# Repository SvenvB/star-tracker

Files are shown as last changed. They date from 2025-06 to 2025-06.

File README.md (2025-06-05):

# DIY Sidereal Star Tracker for the EQ-13 mount (Orion SpaceProbe 130ST telescope)

I'm using the [Orion SpaceProbe 130ST telescope](https://www.highpointscientific.com/orion-spaceprobe-130st-short-tube-eq-reflector-telescope) with a [ZWO ASI224MC](https://www.zwoastro.com/product/zwo-asi224mc/) CMOS imaging camera and enjoy deep-sky imaging without breaking the bank. I got the telescope right before Orion ceased to exist and was therefore unable to purchase their [electronic tracking drive](https://www.amazon.com/Orion-Electronic-Tracking-Drive-Mount/dp/B0B9GHRXKY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) for the [EQ-13 mount](https://optcorp.com/products/orion-eq-13-equatorial-telescope-mount-and-tripod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) that came with the telescope. As a result, I decided to make a simple driver myself. The total price was around $50 (I am not fully sure since I had various components already in house), with the cost dominated by the stepper motor (~$30).

The star tracker is powered by a 12 V source using 8× 1.5 V AA batteries. This power source is also used for my [Flat Frame Light Diffuser](https://github.com/SvenvB/Flat-frame-light-diffuser). The battery pack lasts at least one or two full nights imaging.

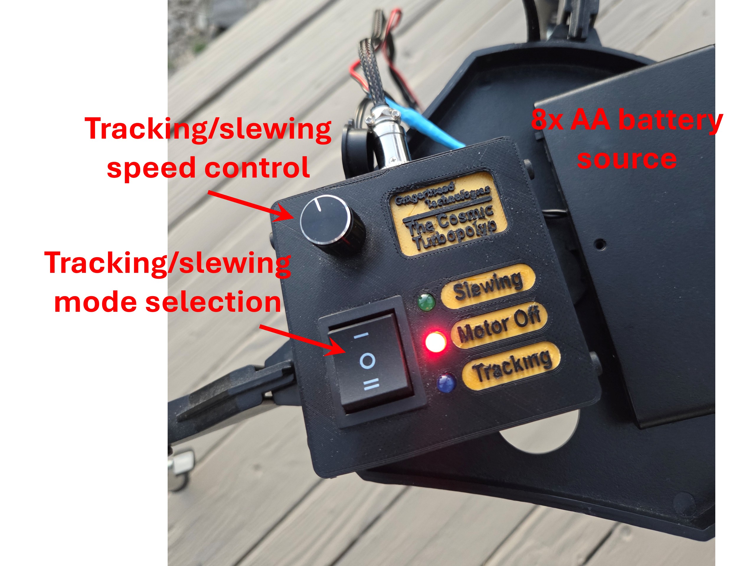
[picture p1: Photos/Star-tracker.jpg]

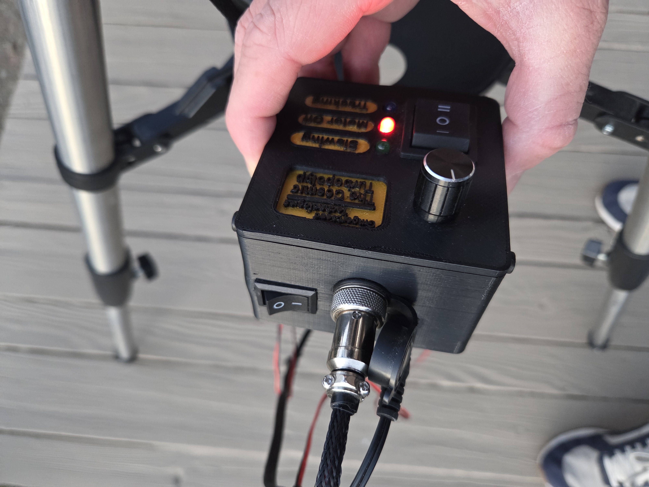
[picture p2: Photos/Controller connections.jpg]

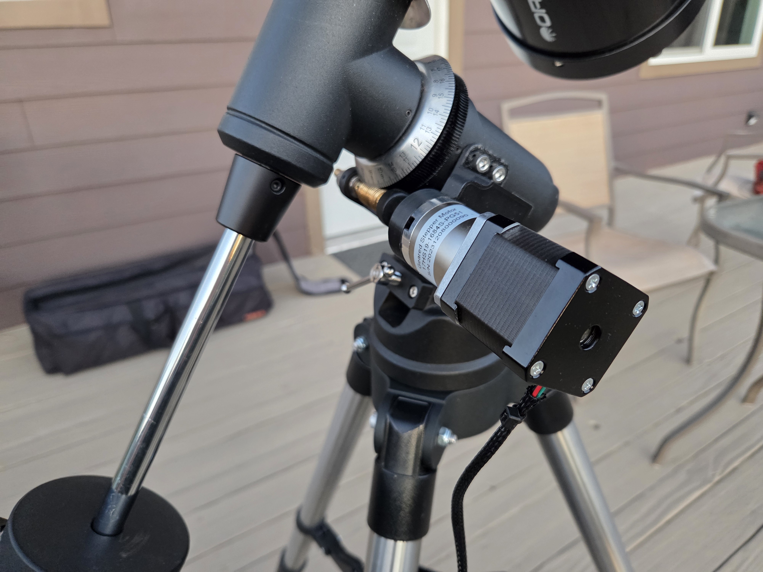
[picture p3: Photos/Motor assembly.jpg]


With this motor, I’ve been able to consistently achieve good tracking for exposure times of up to 5 seconds without noticeable star trailing. For example, see the stacked result of a 140-frame, 5-second exposure of the M27 Dumbbell Nebula:

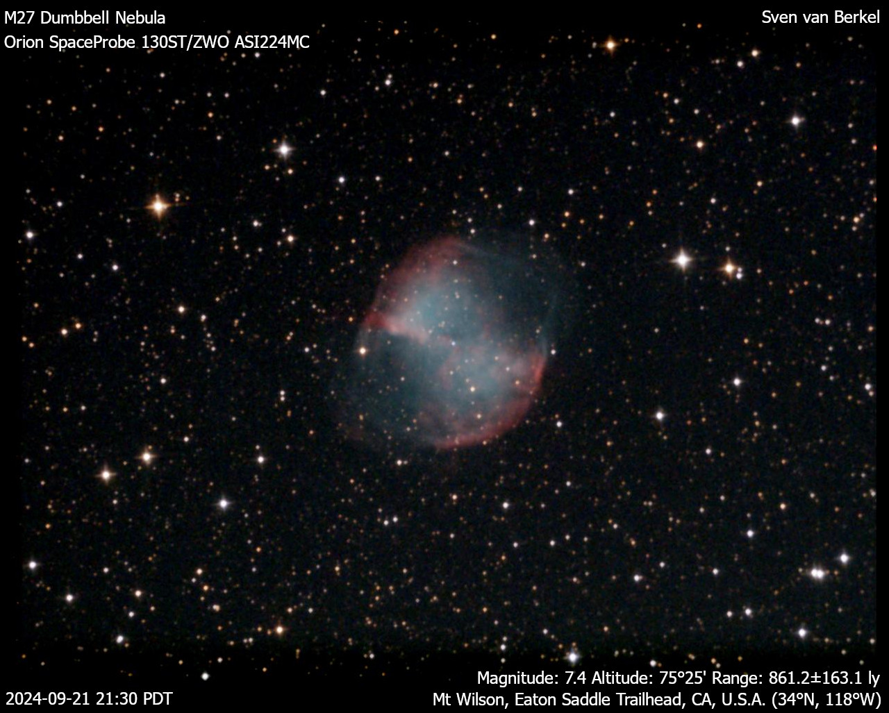
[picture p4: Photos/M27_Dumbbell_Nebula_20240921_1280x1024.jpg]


The exposure time can be pushed up to 20 seconds, as I tried recently when imaging the M51 Whirlpool Galaxy and M104 Sombrero Galaxy. At this exposure time, I had to discard about 50% of the frames due to noticeable star trailing, but the results were still quite nice:

**M51 Whirlpool Galaxy using 49 frames at 20-second exposure:**

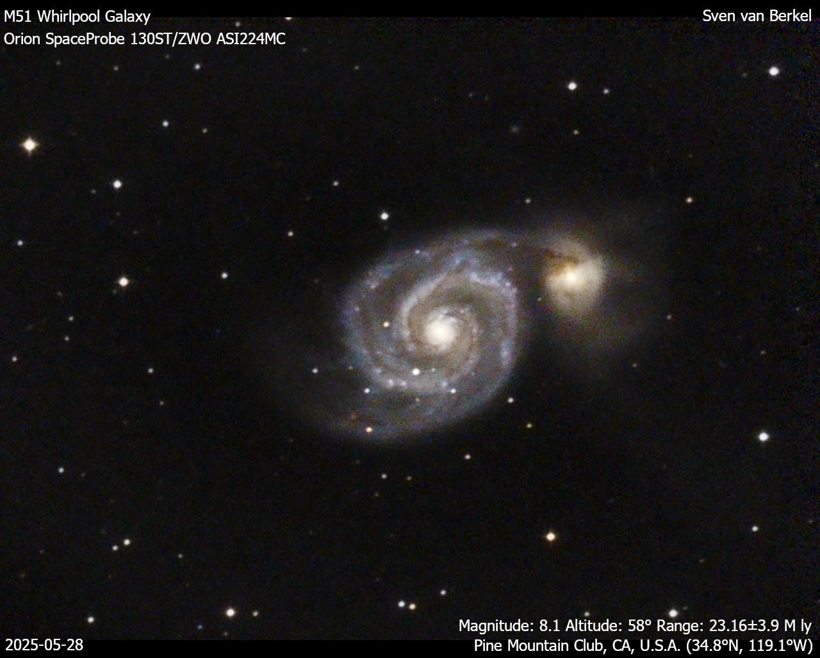
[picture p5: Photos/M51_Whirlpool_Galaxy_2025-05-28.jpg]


**M104 Sombrero Galaxy using 162 frames at 20-second exposure:**

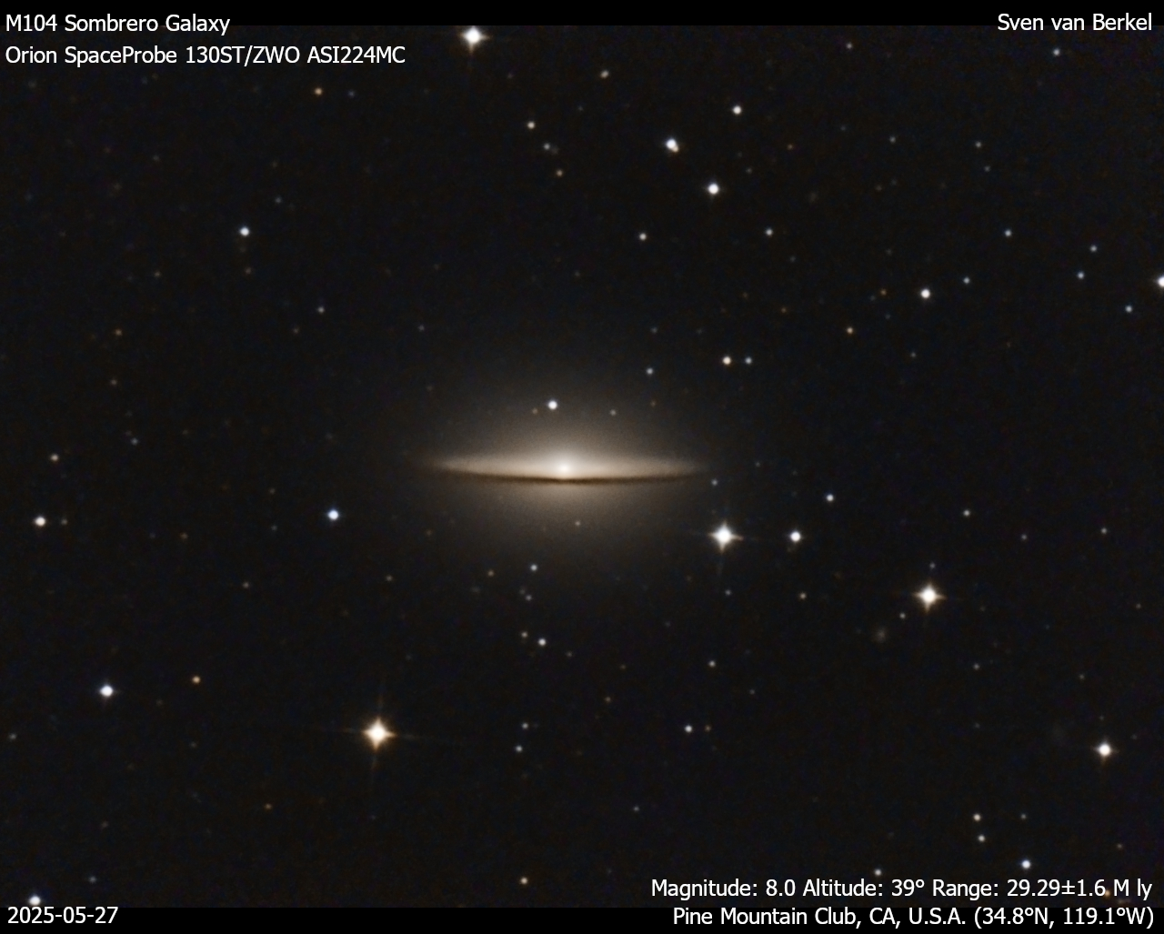
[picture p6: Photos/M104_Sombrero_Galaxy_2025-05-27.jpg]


Keep in mind that the EQ-13 mount is very flimsy, so the effective tracking speed can be inconsistent and occasionally needs to be fine-tuned with the rotary encoder. Properly balancing the telescope with the counterweight is also important.

The star tracker has two modes: **Tracking** (sidereal speed) and **Slewing** (for quick repointing). Both speeds can be fine-tuned with the rotary encoder. Clicking the encoder resets the speed to its default value.

---

## Materials

* **Stepper motor** – The [17HS19-1684S-PG51](https://www.omc-stepperonline.com/nema-17-stepper-motor-bipolar-l-48mm-w-gear-ratio-51-1-planetary-gearbox-17hs19-1684s-pg51) has an 51:1 gear ratio Planetary Gearbox and 0.035 deg / step. 
* **[A4988 stepper motor driver](https://www.aliexpress.us/item/3256805793855652.html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)** - with heatsink  
* **[Arduino Nano](https://www.aliexpress.us/item/3256805941736729.html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)**  
* **KY-040 Rotary Encoder** - with clickable switch
* **[AMS1117-5.0V voltage regulator](https://www.aliexpress.us/item/3256803404676437.html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)**
* **100 uF radial electrolytic capacitor** - for A4988 protection
* **4x through hole 5mm LEDs** - Three to indicate the motor mode and one to indicate that the controller is powered.
* **6x SMD 0805 resistors** - 4x for LED loading (~1 kOhm) and 2x pull-up resistors for the switch (>5 kOhm).
* **2A glass tube fuse and [fuse holder](https://www.amazon.com/dp/B074N1NMMX?ref_=ppx_hzsearch_conn_dt_b_fed_asin_title_1)** - for A4988 protection. The holder has 15mm pin spacing and can hold a 5x20mm fuse.
* **[5.5x2.1mm DC barrel jack](https://www.amazon.com/dp/B081DYQSC9/ref=pe_386300_440135490_TE_simp_item_image?th=1)** - for controller power supply
* **[4 pin aviation plug](https://www.amazon.com/dp/B07ZP725YD/ref=pe_386300_440135490_TE_simp_item_image)** - for connecting the stepper motor
* **[3 position rocker switch](https://www.aliexpress.us/item/2251832521009333.html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)** - for motor mode selection
* **2 position rocker switch** - for controller power ON/OFF
* **2x 5-pin JST connectors** - male and female for connecting the rotary encoder and Switch-and-LED board
* **2x 2-pin JST connectors** - male and female for connecting the power rocker switch and power to the Switch-and-LED board.
* **4-pin JST connector**  - male and female for connecting the aviation plug.
* **[8x AA battery holder](https://www.amazon.com/dp/B09LTSNJTW/ref=pe_386300_440135490_TE_simp_item_image)** - with 5.5x2.1mm Male Jack Connector
* **various screws** - to mount the PCBs to the casing and top-plate, to mount the top-plate to the casing, to connect the stepper motor to the 3D-printed mount, to prevent the 3D-printed coupling piece from slipping on the worm gear shaft, to connect the 3D-printed mount to the EQ-13 body.
* **3D printer and filament** - for the motor mount and controller box.

**Optional**
* **Capacitors** - at the output of the voltage regulator to reduce power supply noise. I used a 10 uF radial and 100 nF + 10 nF ceramic disc capacitors in parallel. 
* **Cable sleeve** - to organize the stepper motor wires.
* **3-pin screw terminal** - mounted on the switch-and-LED board, to easily connect and disconnect the 3-position rocker switch.

---

## Instructions

### 1. Calculate Stepper Motor Requirements

- Stepper motors are highly accurate and provide high torque, making them ideal for this application. A typical stepper motor has 200 steps per revolution (1.8°/step).
- I tested that the Right Ascension (RA) knob on the EQ-13 mount must be rotated about 5.5 times to move 1 hour in RA. This corresponds to roughly 132 revolutions over 24 h in RA, i.e., a worm gear ratio of 132:1.
- One sidereal day is 23h 56m 4s, or 86,164 seconds. Therefore, the worm gear should rotate at ~0.55°/s. Since a typical stepper motor would move only once every 3+ seconds at this rate, a gearbox is needed.
- Choosing a low gear ratio results in jerky tracking, while too high a gear ratio limits slewing speed.
- I chose the [17HS19-1684S-PG51](https://www.omc-stepperonline.com/nema-17-stepper-motor-bipolar-l-48mm-w-gear-ratio-51-1-planetary-gearbox-17hs19-1684s-pg51) stepper motor with a 51:1 gearbox. This gives a tracking speed of ~15.6 steps per second, which I would not recommend going below.

**RA worm gear visible in the picture below:**

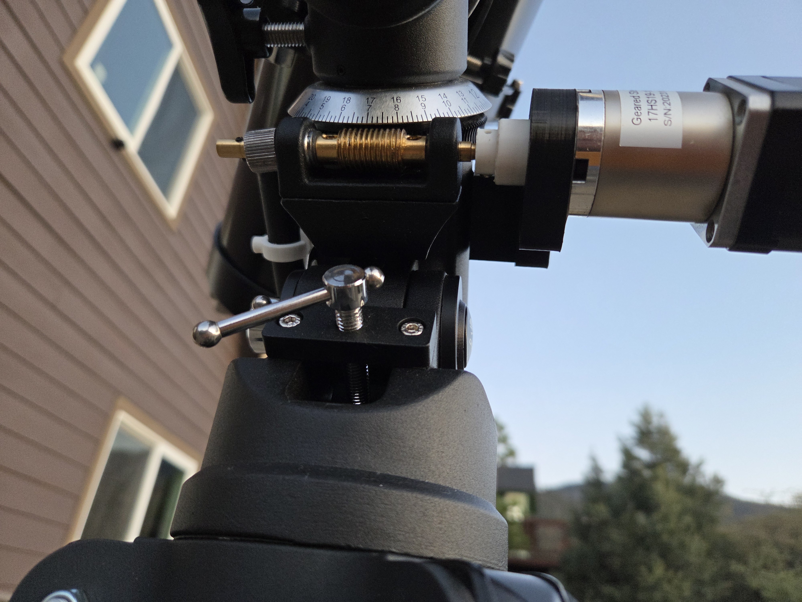
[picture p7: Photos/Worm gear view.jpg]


---

### 2. Electrical Design

The controller uses two PCBs:

1. **Switch-and-LED board** – Mounted to the front plate. This board connects to the 3-position rocker switch, integrates pull-up resistors, and drives LEDs indicating the motor mode. It is reused from another project that daisy-chains the power pins two multiple boards.
2. **Controller board** – Mounted to the bottom of the casing. This board contains the Arduino, stepper motor driver, and supporting components.

Boards were designed in KiCAD. Gerber files are attached, and PCBs were ordered via JLCPCB.

#### Switch-and-LED Board
* The pin-headers shown below are not needed. You can directly solder the cables to the PCB, as is shown in the *Assembled Control Box* photograph in Section 4 below. 
* The schematic indicates LED resistors of 470 Ohm. However, I have found that the LEDs are too bright with those values. I recommend increasing them. 

*KiCAD Schematic:*
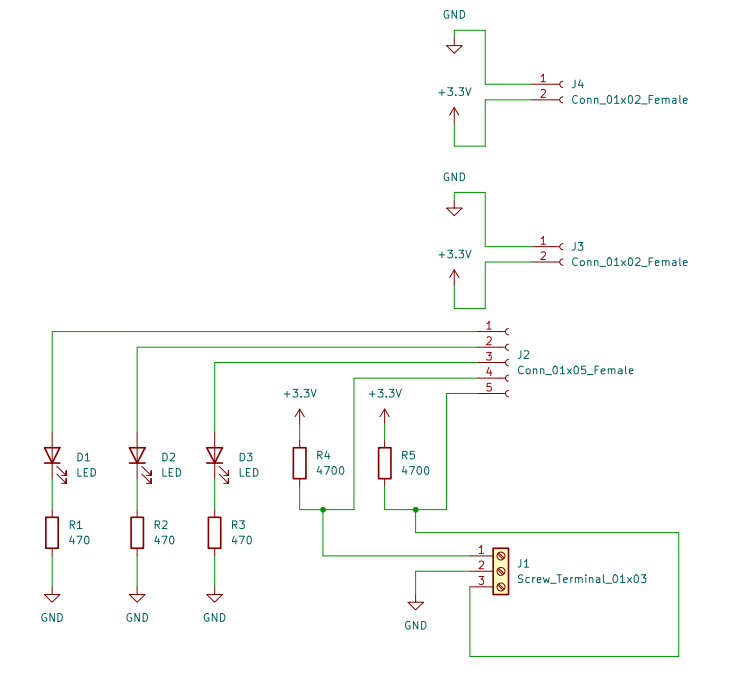
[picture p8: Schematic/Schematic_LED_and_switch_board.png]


*KiCAD 3D View:*
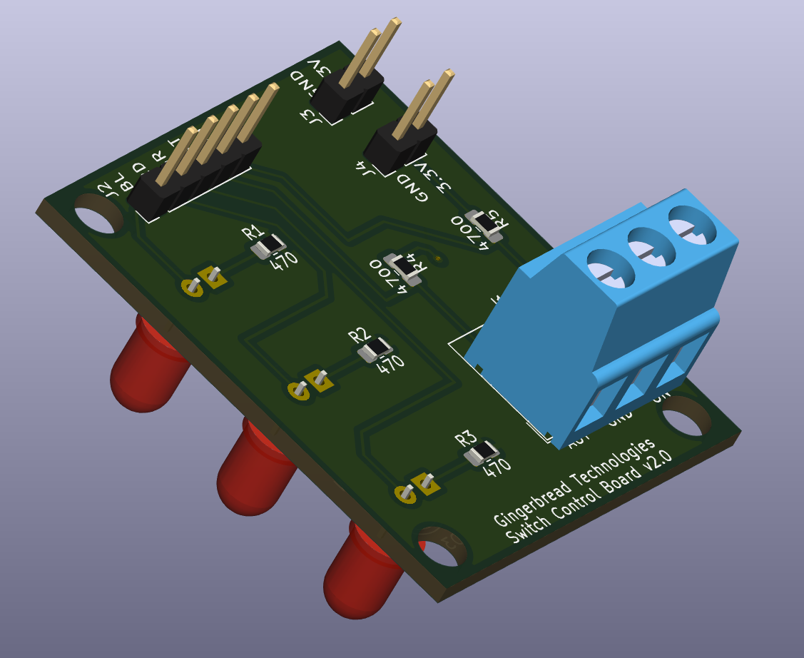
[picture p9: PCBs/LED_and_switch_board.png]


#### Controller Board

- Be sure to include the 100 µF capacitor. The A4988 can produce voltage spikes due to back-EMF from the stepper motor’s inductance. This capacitor helps absorb those spikes, protecting the driver. Place the capacitor as close to the driver as is possible.
- The capacitors at the AMS1117 output are optional.
- Use the method described [here](https://www.pololu.com/product/1182) to limit the A4988 current to your motor’s rated current (1.68 A/phase for mine).
- I have not employed microstepping to increase the number of steps per second. The motor might operate more smoothly if we half the step. However, it will mean tighter timing and more processing overhead for the Arduino, and a reduced torque per microstep. If the mount is imbalanced the torque might not be adequate. Something to be tested.

*KiCAD Schematic:*
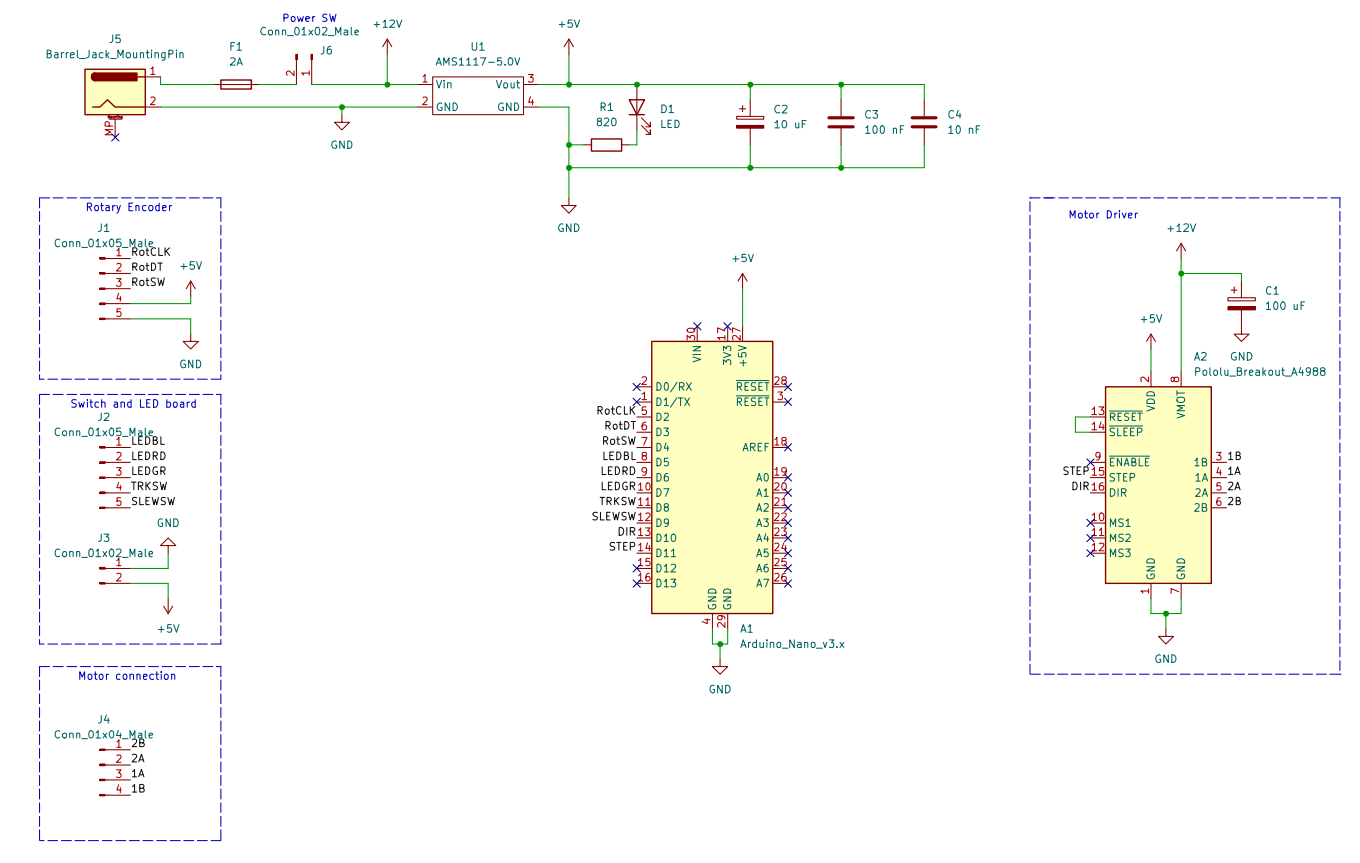
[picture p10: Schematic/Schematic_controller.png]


*KiCAD 3D View:*
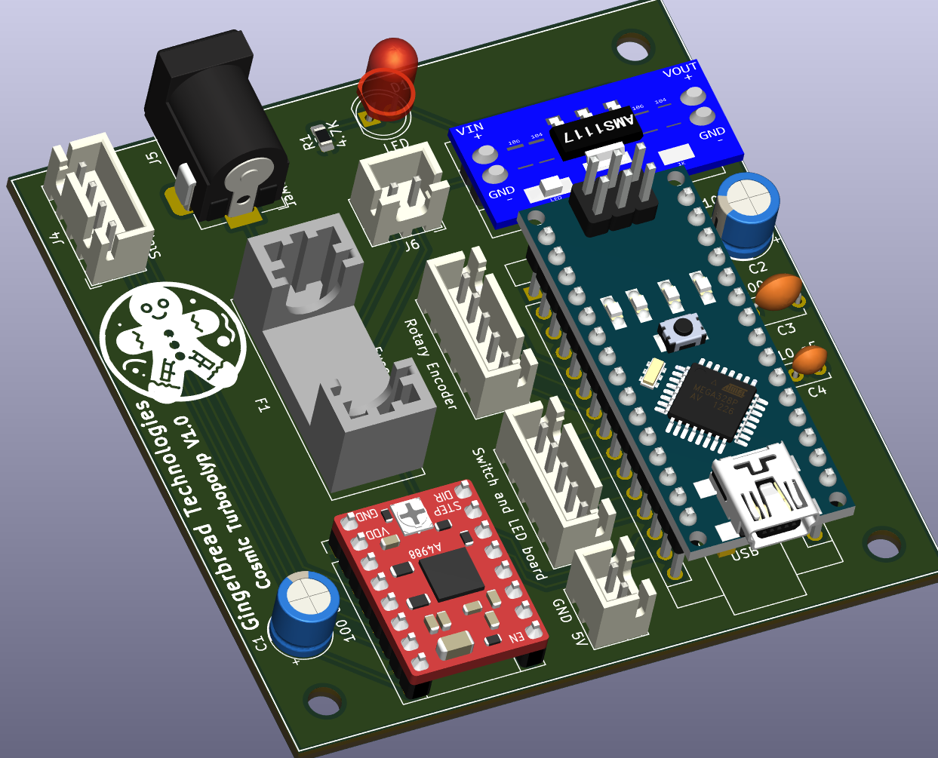
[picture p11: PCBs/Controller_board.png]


*Assembled Controller Photo:*
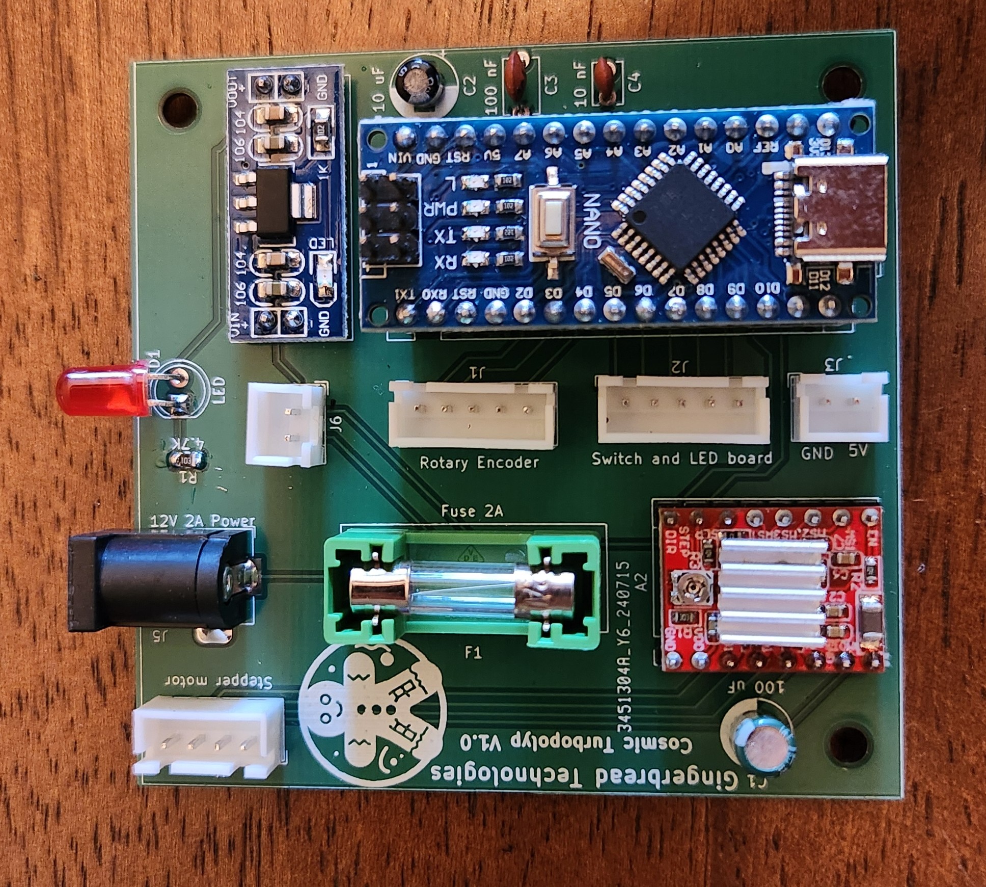
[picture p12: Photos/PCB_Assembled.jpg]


---

### 3. CAD Design

- The control box and motor mount were designed in FreeCAD. Design files and .STLs are attached.
- The coupling piece between the stepper motor and worm gear shaft (green part in the image) must fit very tightly to avoid backlash.
- You will need a screw to mate the coupling piece to the worm gear shaft. 

*FreeCAD View – Control Box (Closed):*
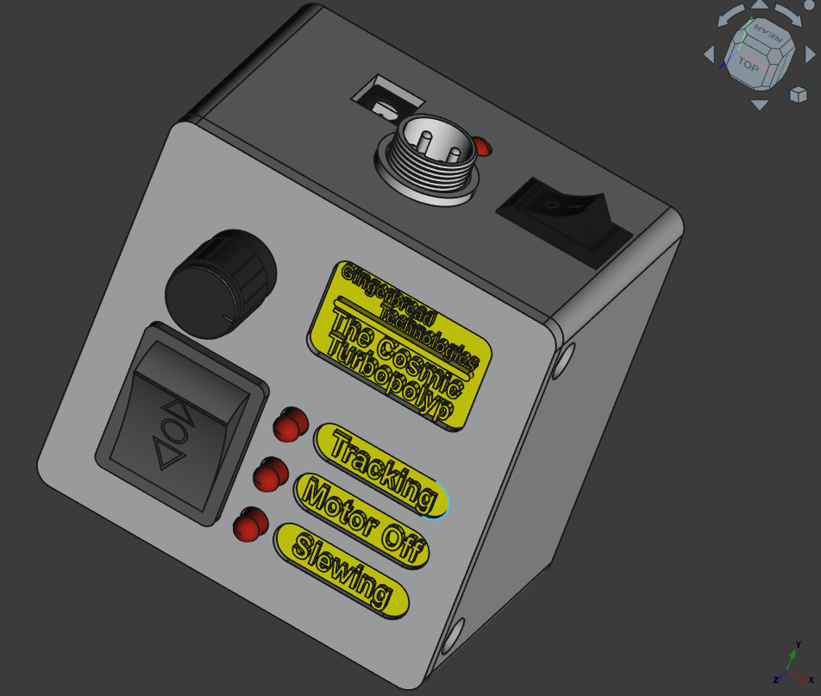
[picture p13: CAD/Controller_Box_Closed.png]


*FreeCAD View – Control Box (Open):*
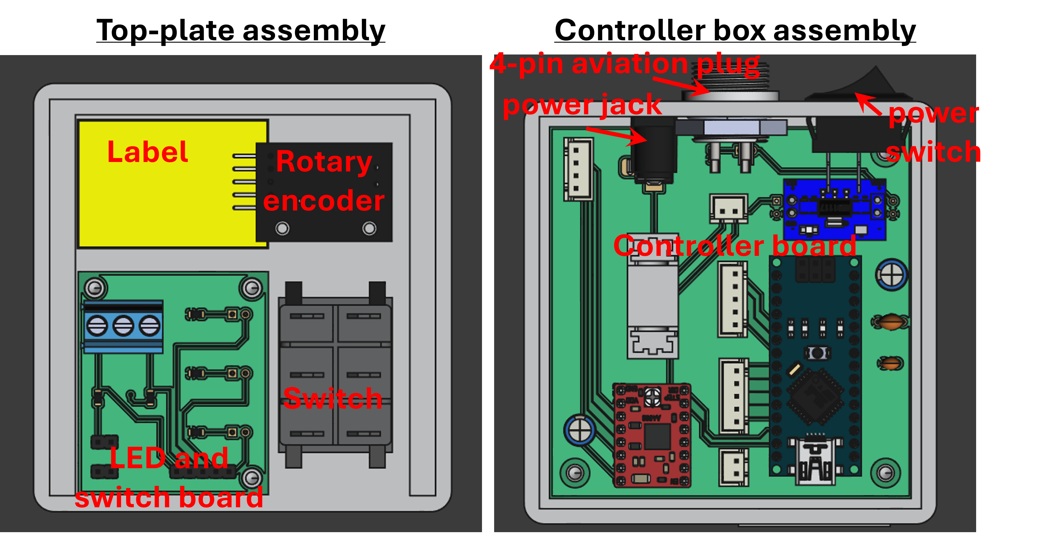
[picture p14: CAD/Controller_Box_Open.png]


*FreeCAD View – Motor Mount:*
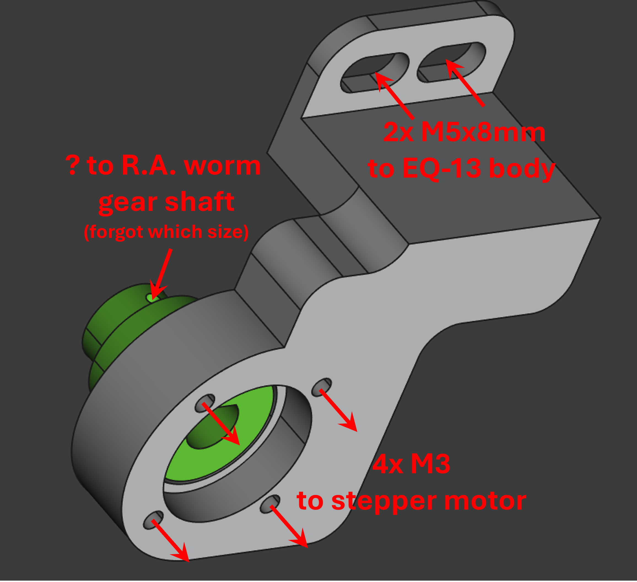
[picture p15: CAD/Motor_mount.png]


---

### 4. Assembly

- Mount the PCBs to the casing and top plate using screws.
- Avoid contact between wires and the heatsink of the stepper motor driver.

*Assembled Control Box:*
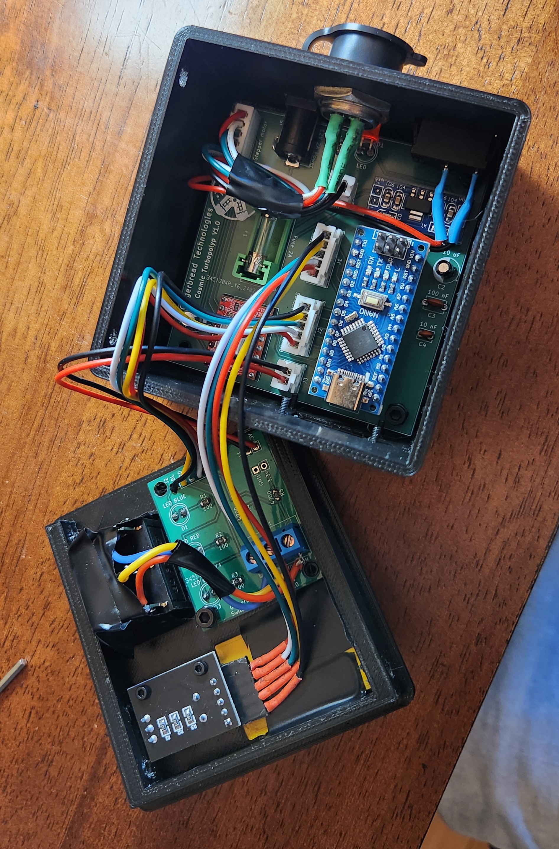
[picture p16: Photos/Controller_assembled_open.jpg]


*Assembled Stepper Motor:*


---

### 5. Arduino Coding and Operation

- The Arduino is programmed using the standard Arduino IDE. Code is available [here](./Arduino/RA_Controller_V3/RA_Controller_V3.ino).
- I found the most stable tracking at 16.3 steps/second, close to the calculated 15.6 steps/sec sidereal speed.
- In **Tracking mode**, each rotary tick changes the speed by ±0.1 steps/sec.
- In **Slewing mode**, each tick changes the speed by ±1× sidereal rate. Slewing is possible in both RA directions.
- Clicking the rotary encoder resets the speed to its default value.

**Clear skies!**

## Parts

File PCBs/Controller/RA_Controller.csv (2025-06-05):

Reference | Value | Datasheet | Footprint | Qty | DNP
A1 | Arduino_Nano_v3.x | http://www.mouser.com/pdfdocs/Gravitech_Arduino_Nano3_0.pdf | Module:Arduino_Nano | 1
A2 | Pololu_Breakout_A4988 | https://www.pololu.com/product/2980/pictures | Module:Pololu_Breakout-16_15.2x20.3mm | 1
C1 | 100 uF | ~ | Capacitor_THT:CP_Radial_D6.3mm_P2.50mm | 1
C2 | 10 uF | ~ | Capacitor_THT:CP_Radial_D6.3mm_P2.50mm | 1
C3 | 100 nF | ~ | Capacitor_THT:C_Disc_D5.1mm_W3.2mm_P5.00mm | 1
C4 | 10 nF | ~ | Capacitor_THT:C_Disc_D3.8mm_W2.6mm_P2.50mm | 1
D1 | LED | ~ | LED_THT:LED_D5.0mm | 1
F1 | 2A | ~ | LED_THT:LED_D5.0mm | 1
J1,J2 | Conn_01x05_Male | ~ | Connector_JST:JST_XH_B5B-XH-A_1x05_P2.50mm_Vertical | 2
J3,J6 | Conn_01x02_Male | ~ | Connector_JST:JST_XH_B2B-XH-A_1x02_P2.50mm_Vertical | 2
J4 | Conn_01x04_Male | ~ | Connector_JST:JST_XH_B4B-XH-A_1x04_P2.50mm_Vertical | 1
J5 | Barrel_Jack_MountingPin | ~ | Connector_BarrelJack:BarrelJack_Horizontal | 1
R1 | 820 | ~ | Resistor_SMD:R_0805_2012Metric_Pad1.20x1.40mm_HandSolder | 1
U1 | AMS1117-5.0V |  | Svens Custom Footprints:AMS1117-5.0V | 1

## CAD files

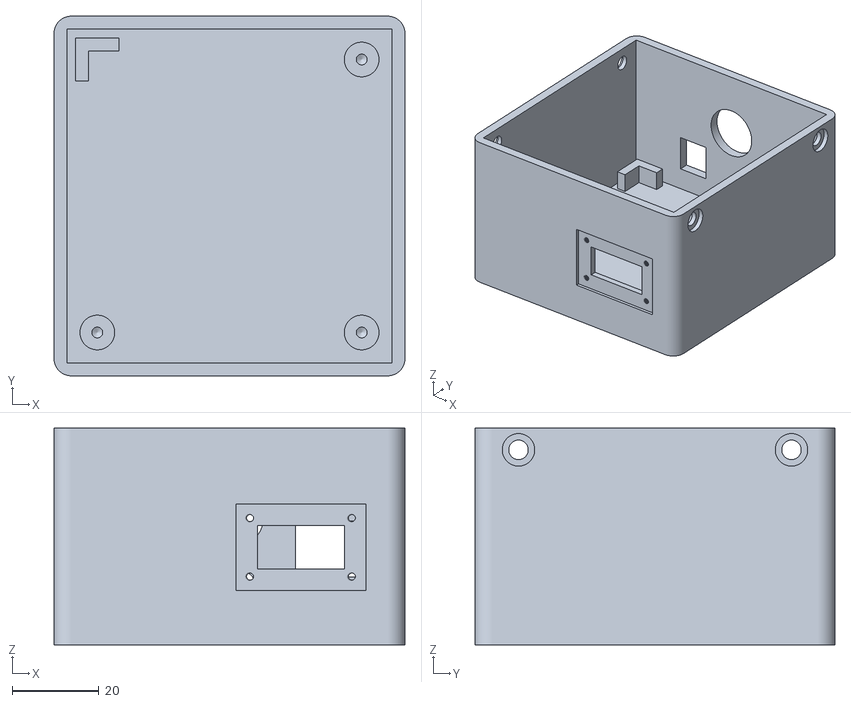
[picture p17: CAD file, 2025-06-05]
CAD/STLs/Main_box.stl
81.0 x 83.0 x 50.0

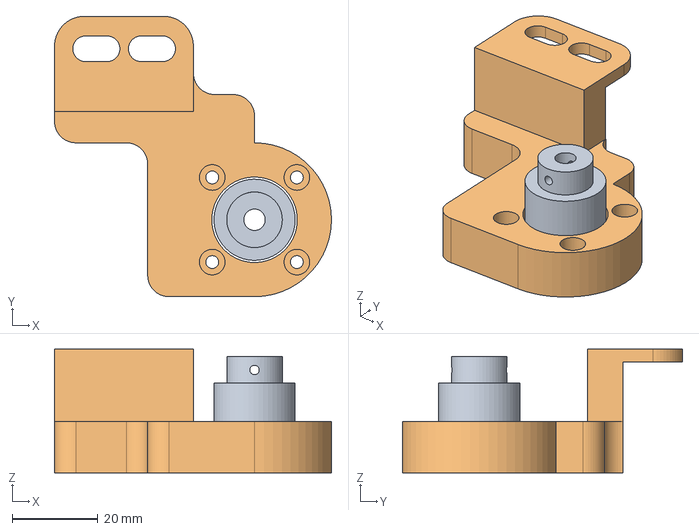
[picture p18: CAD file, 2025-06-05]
CAD/FreeCAD/MotorMount_V2.FCStd
64.8 x 65.6 x 29.0 mm
Stepper_to_RA_knob
Stepper_mount

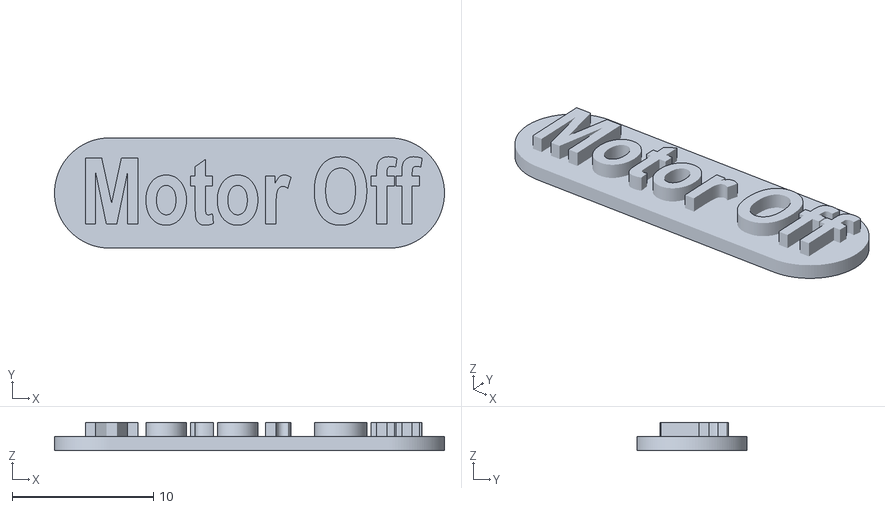
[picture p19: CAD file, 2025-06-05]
CAD/STLs/Motor_off_label.stl
27.6 x 7.80 x 2.00

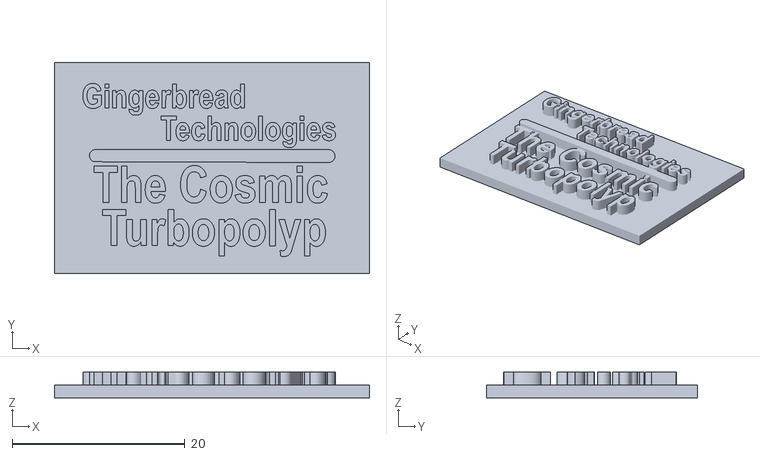
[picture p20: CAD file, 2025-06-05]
CAD/STLs/Gingerbread_label.stl
36.5 x 24.5 x 3.00

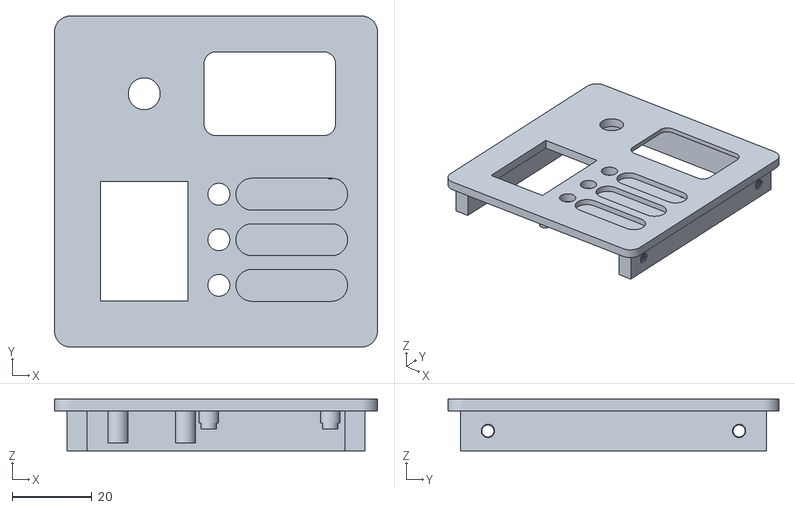
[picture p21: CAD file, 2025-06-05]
CAD/STLs/Top_plate.stl
81.0 x 83.0 x 13.0

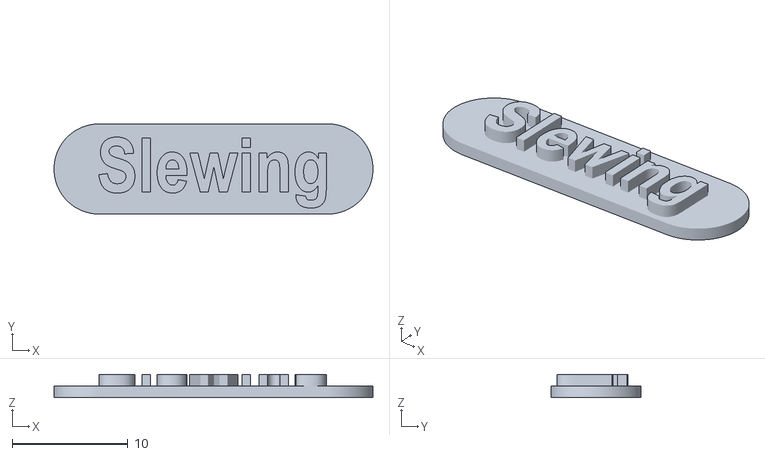
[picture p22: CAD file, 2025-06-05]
CAD/STLs/Slewing_label.stl
27.6 x 7.80 x 2.00

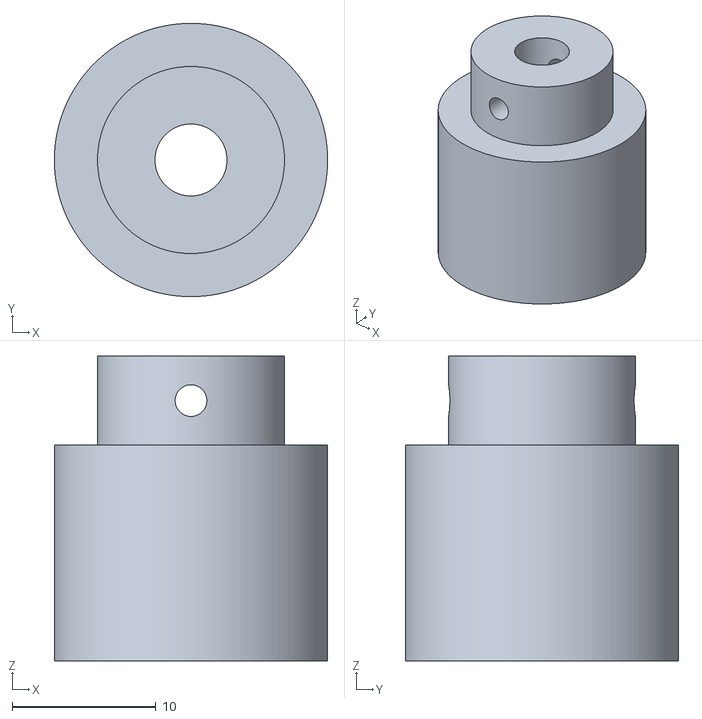
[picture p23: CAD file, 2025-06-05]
CAD/STLs/Stepper_to_RA_knob_V2.stl
19.0 x 19.0 x 21.2

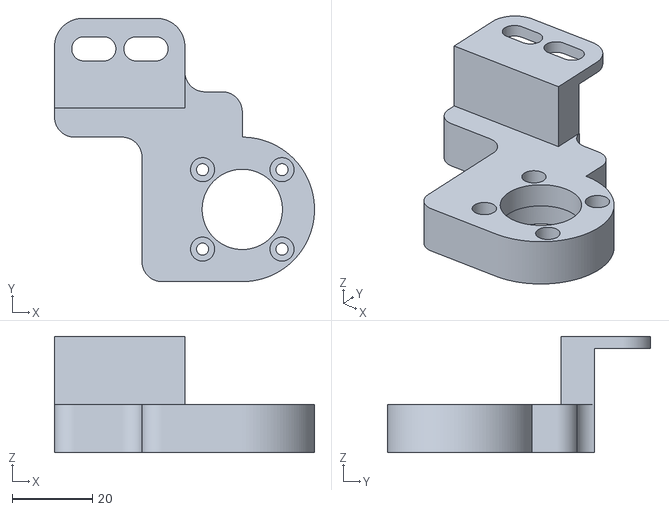
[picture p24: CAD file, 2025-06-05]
CAD/STLs/Stepper_Mount.stl
64.8 x 65.6 x 29.0

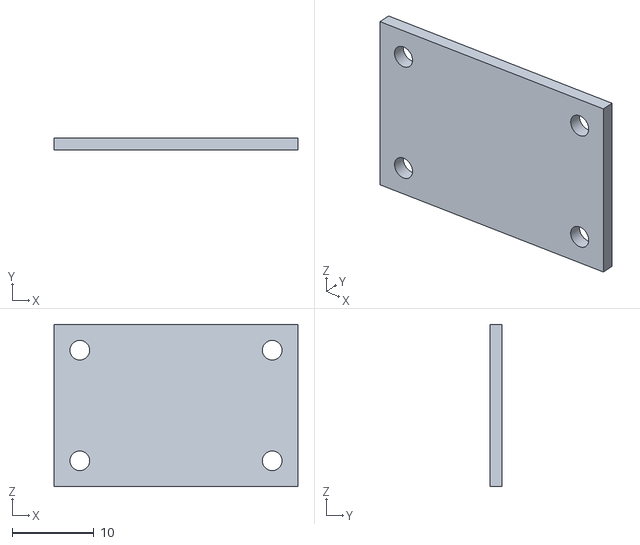
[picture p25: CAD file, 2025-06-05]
CAD/STLs/USB_plate.stl
29.8 x 1.50 x 19.8

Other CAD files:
CAD/STLs/Tracking_label.stl

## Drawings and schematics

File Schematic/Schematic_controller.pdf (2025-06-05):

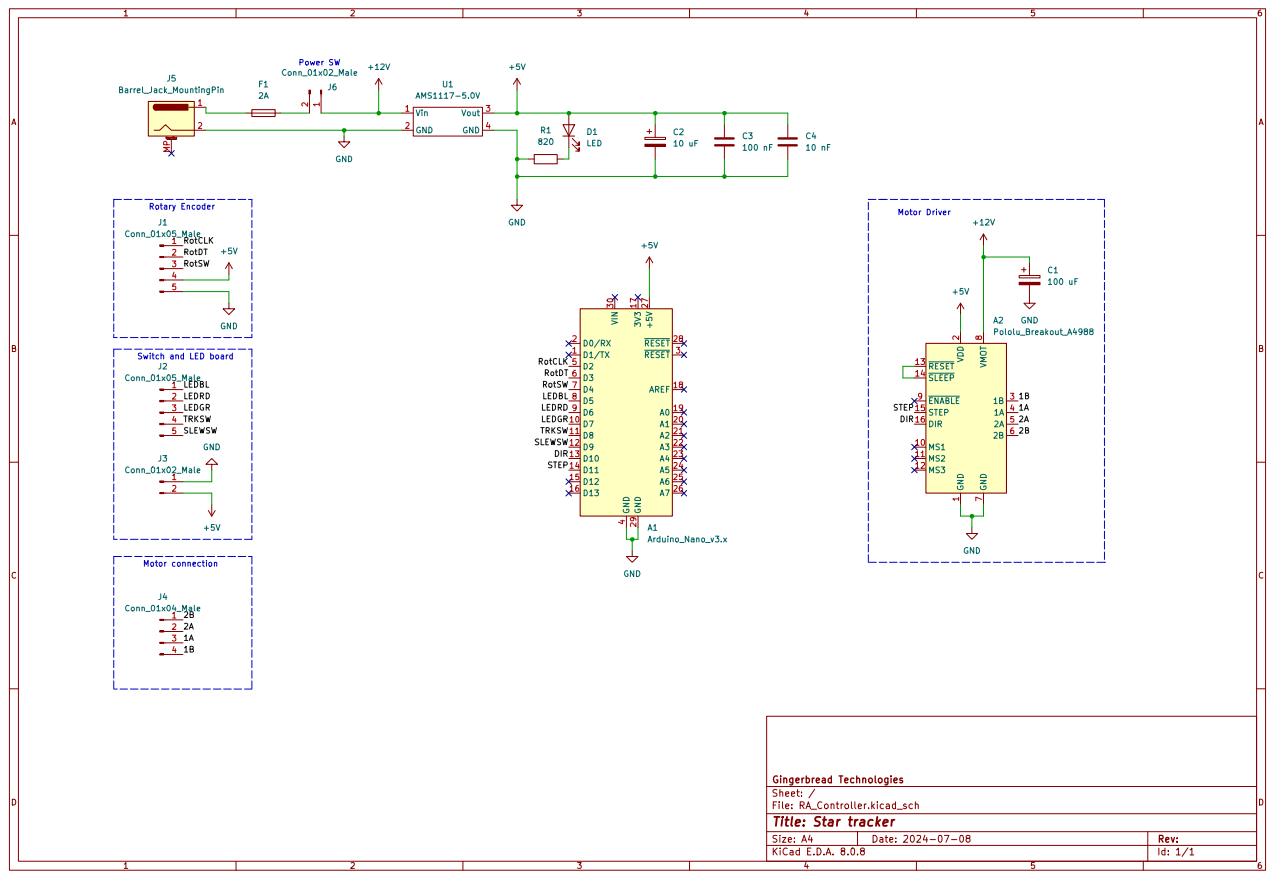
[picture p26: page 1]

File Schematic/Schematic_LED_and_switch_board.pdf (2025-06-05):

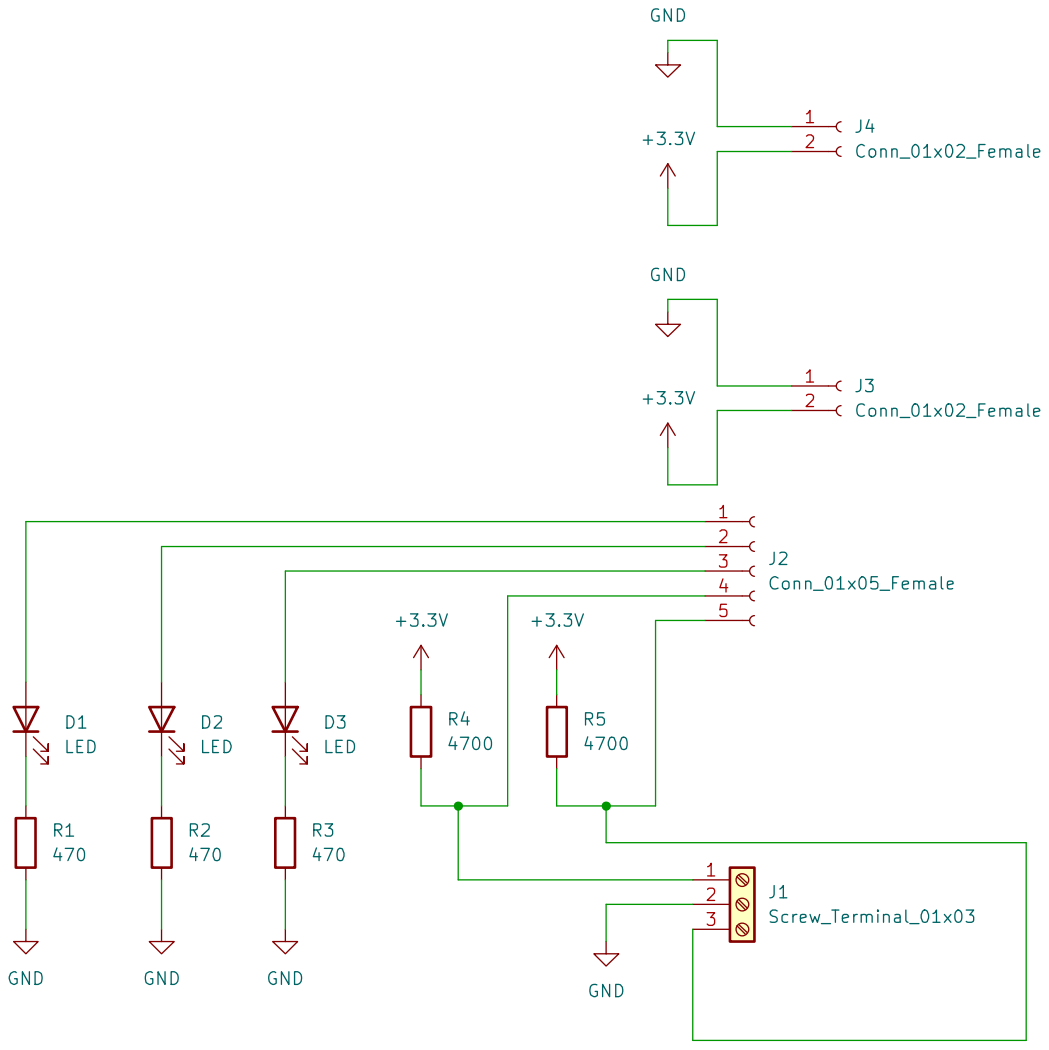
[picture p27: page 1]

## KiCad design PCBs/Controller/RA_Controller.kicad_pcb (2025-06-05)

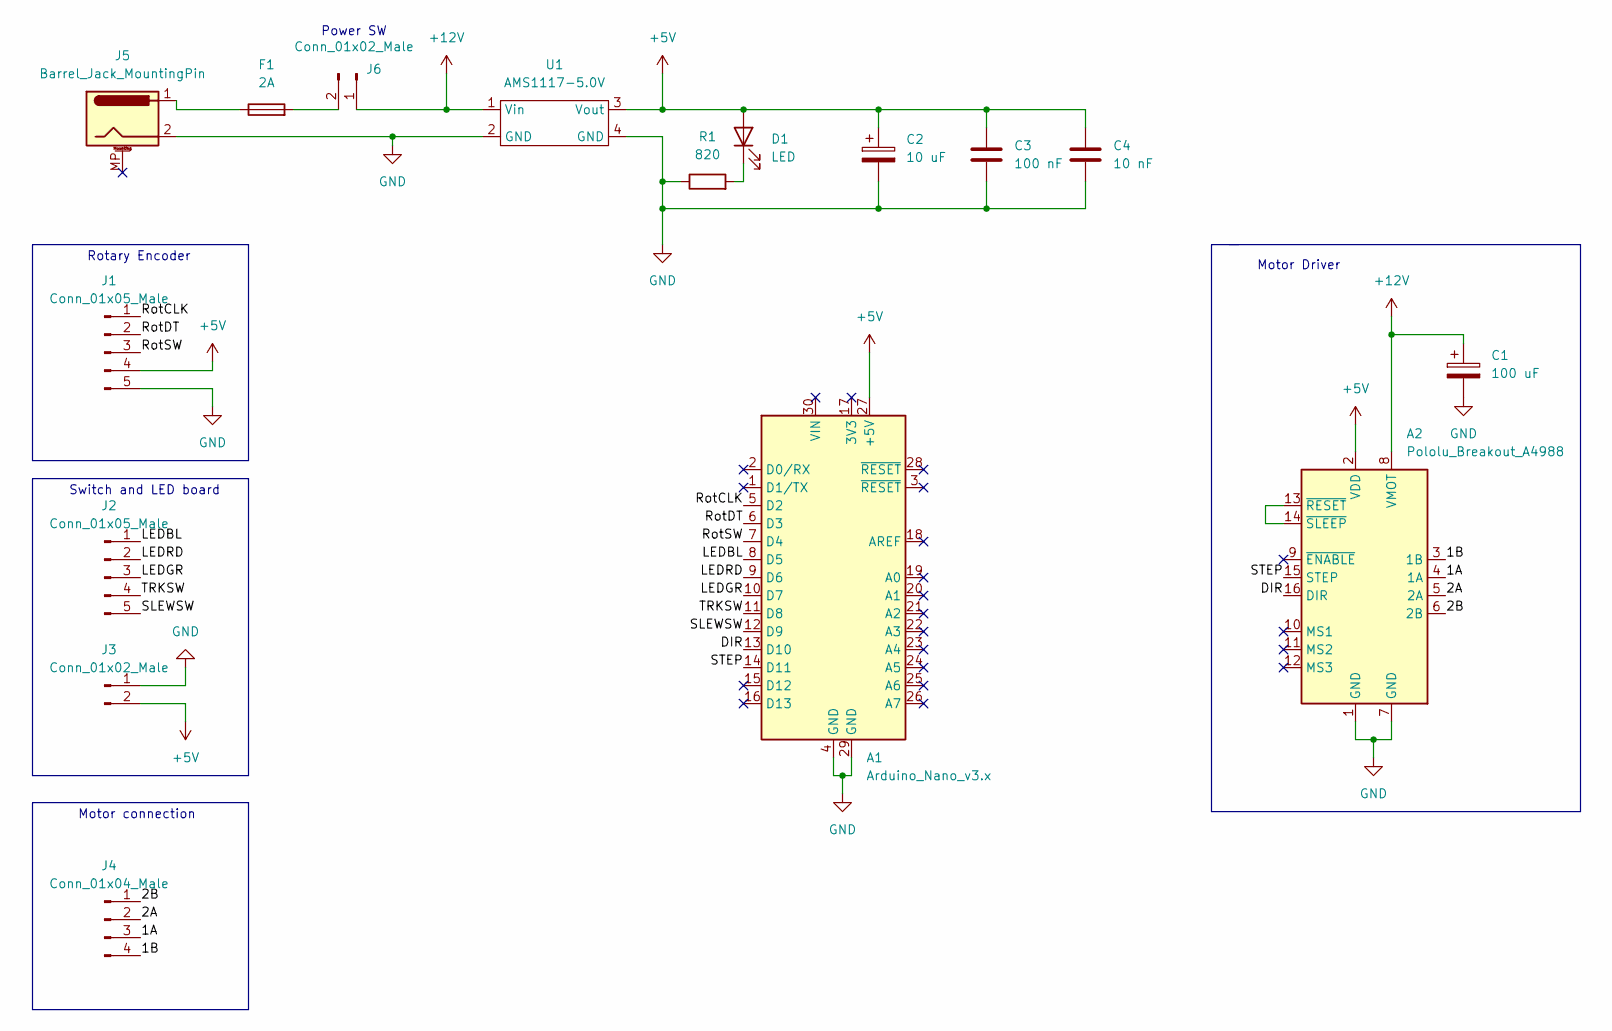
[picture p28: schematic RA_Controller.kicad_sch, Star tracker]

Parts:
A1: Arduino_Nano_v3.x; Arduino_Nano
A2: Pololu_Breakout_A4988; Pololu_Breakout-16_15.2x20.3mm
C1: 100 uF; CP_Radial_D6.3mm_P2.50mm
C2: 10 uF; CP_Radial_D6.3mm_P2.50mm
C3: 100 nF; C_Disc_D5.1mm_W3.2mm_P5.00mm
C4: 10 nF; C_Disc_D3.8mm_W2.6mm_P2.50mm
D1: LED; LED_D5.0mm
F1: 2A; LED_D5.0mm
J1, J2: Conn_01x05_Male; JST_XH_B5B-XH-A_1x05_P2.50mm_Vertical
J3, J6: Conn_01x02_Male; JST_XH_B2B-XH-A_1x02_P2.50mm_Vertical
J4: Conn_01x04_Male; JST_XH_B4B-XH-A_1x04_P2.50mm_Vertical
J5: Barrel_Jack_MountingPin; BarrelJack_Horizontal
R1: 820; R_0805_2012Metric_Pad1.20x1.40mm_HandSolder
U1: AMS1117-5.0V

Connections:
+5V: A1.27 (+5V), A2.2 (VDD), C2.1, C3.1, C4.1, D1.2 (A), J1.4, J3.2, U1.3 (Vout)
+12V: A2.8 (VMOT), C1.1, J6.1, U1.1 (Vin)
/1A: A2.4 (1A), J4.3
/1B: A2.3 (1B), J4.4
/2A: A2.5 (2A), J4.2
/2B: A2.6 (2B), J4.1
/DIR: A1.13 (D10), A2.16 (DIR)
/LEDBL: A1.8 (D5), J2.1
/LEDGR: A1.10 (D7), J2.3
/LEDRD: A1.9 (D6), J2.2
/RotCLK: A1.5 (D2), J1.1
/RotDT: A1.6 (D3), J1.2
/RotSW: A1.7 (D4), J1.3
/SLEWSW: A1.12 (D9), J2.5
/STEP: A1.14 (D11), A2.15 (STEP)
/TRKSW: A1.11 (D8), J2.4
GND: A1.4 (GND), A1.29 (GND), A2.1 (GND), A2.7 (GND), C1.2, C2.2, C3.2, C4.2, J1.5, J3.1, J5.2, R1.1, U1.2 (GND), U1.4 (GND)
unnamed: A2.13 (~RESET), A2.14 (~SLEEP)
unnamed: D1.1 (K), R1.2
unnamed: F1.1, J5.1
unnamed: F1.2, J6.2

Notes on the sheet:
Motor connection
Motor Driver
Switch and LED board
Power SW
Rotary Encoder

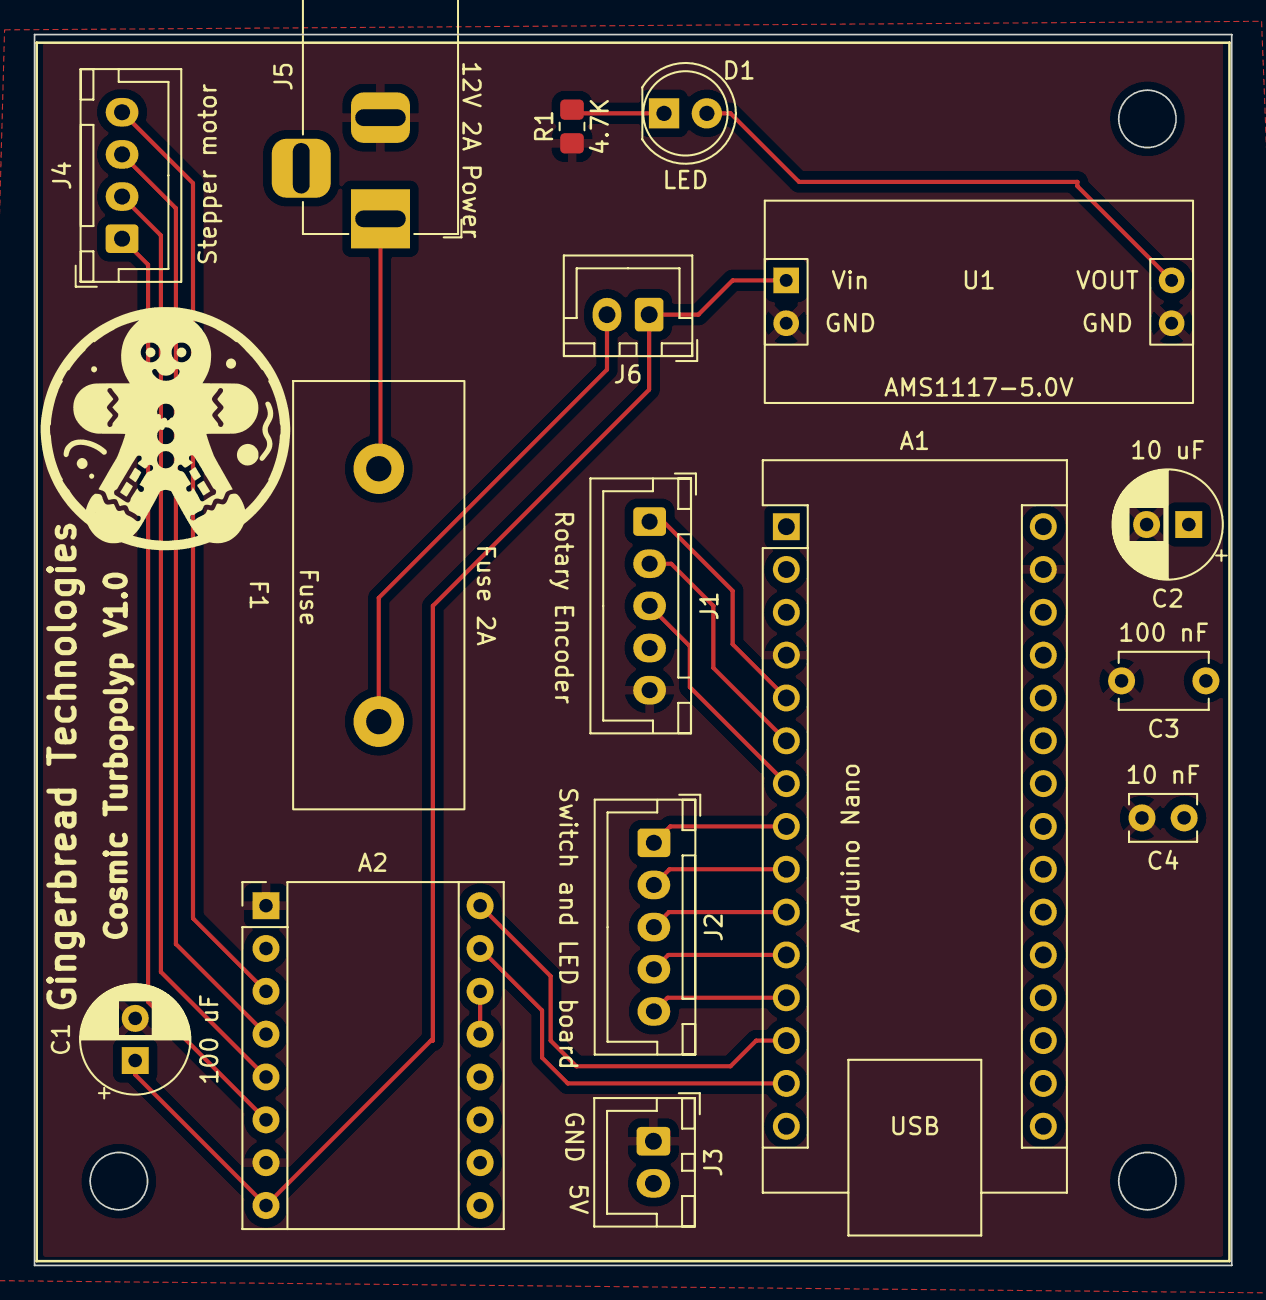
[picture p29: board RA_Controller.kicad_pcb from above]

Board: 2 copper layers, 71.0 x 73.0 mm, 16 parts (0 on the bottom side), 21 nets.

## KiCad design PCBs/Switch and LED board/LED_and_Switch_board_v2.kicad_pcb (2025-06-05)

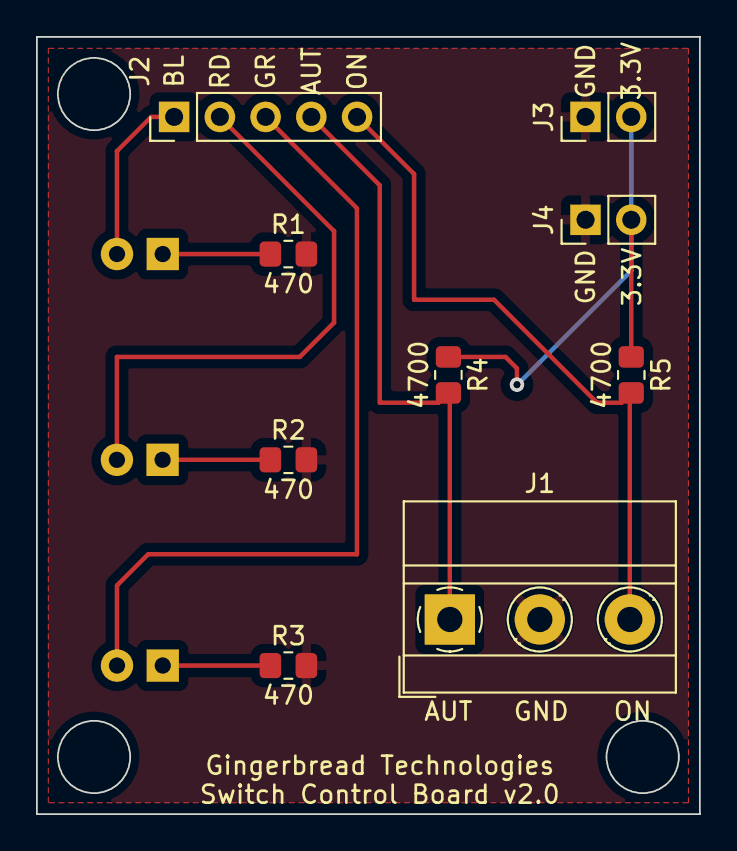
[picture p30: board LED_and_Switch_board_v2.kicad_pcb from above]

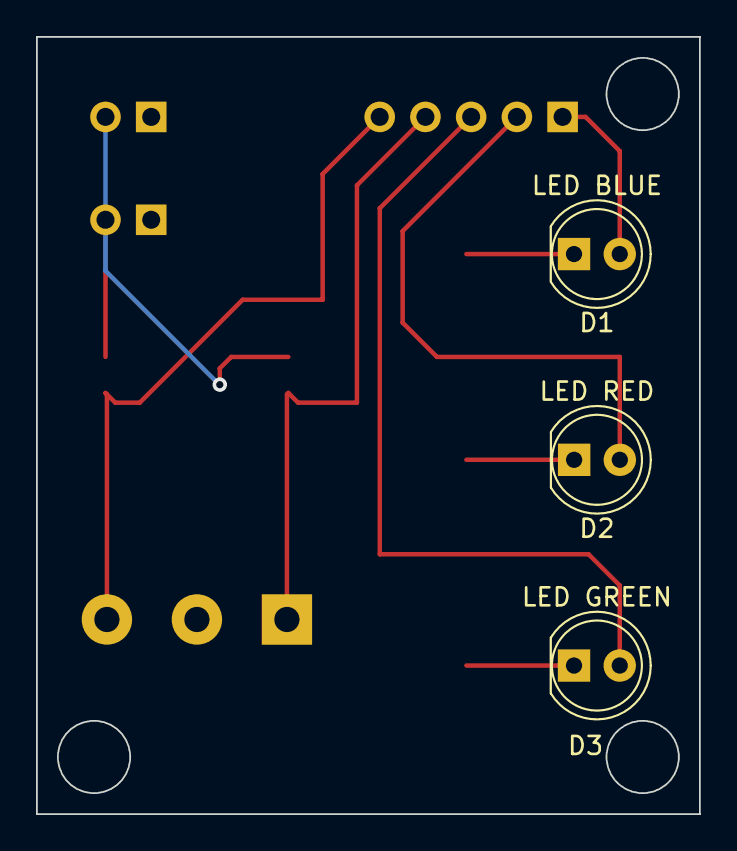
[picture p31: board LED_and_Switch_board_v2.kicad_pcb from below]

Board: 2 copper layers, 36.8 x 43.2 mm, 12 parts (3 on the bottom side), 10 nets.

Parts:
D1: LED BLUE; LED_D5.0mm
D2: LED RED; LED_D5.0mm
D3: LED GREEN; LED_D5.0mm
J1: Screw_Terminal_01x03; TerminalBlock_MetzConnect_Type011_RT05503HBWC_1x03_P5.00mm_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
J2: Conn_01x05_Female; PinHeader_1x05_P2.54mm_Vertical
J3, J4: Conn_01x02_Female; PinHeader_1x02_P2.54mm_Vertical
R1, R2, R3: 470; R_0805_2012Metric_Pad1.20x1.40mm_HandSolder
R4, R5: 4700; R_0805_2012Metric_Pad1.20x1.40mm_HandSolder

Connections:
+3.3V: J3.2, J4.2, R4.1, R5.1
GND: J1.2, J3.1, J4.1, R1.2, R2.2, R3.2
unnamed: D1.1 (K), R1.1
unnamed: D1.2 (A), J2.1
unnamed: D2.1 (K), R2.1
unnamed: D2.2 (A), J2.2
unnamed: D3.1 (K), R3.1
unnamed: D3.2 (A), J2.3
unnamed: J1.1, J2.4, R4.2
unnamed: J1.3, J2.5, R5.2

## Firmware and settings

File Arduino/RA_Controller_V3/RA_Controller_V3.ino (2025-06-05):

#include <AccelStepper.h>

// LEDs
#define LED_tracking 5
#define LED_OFF 6
#define LED_slewing 7

// pins for rotary encoder
#define encoderDT 3
#define encoderCLK 2 // Interrupt
#define encoderSW 4
int previousDT_val;
int previousCLK_val;
int previousSW_val;

// pins for stepper motor
#define stepPin 11
#define dirPin 10 

// input buttons
#define slewing_SW 8
#define tracking_SW 9
int previous_slewing_SW_val;
int previous_tracking_SW_val;

float sidereal_step_per_second = -16.3;  // Initial speed for tracking (steps/sec)
float tracking_rotary_change_sps = -0.1; // Every rotary step is a change of rotary_multiplier step/sec in case of tracking mode
float slewing_step_per_second = 0;  // Initial speed for slewing (steps/sec)
float slewing_rotary_change_sps = sidereal_step_per_second; // Every rotary step is a change of rotary_multiplier step/sec in case of slewing mode  (this was -50 in the first version)

float steps_per_second = 0; // Initialization actual speed of stepper motor
float max_steps_per_second = 1000; // Maximum speed possible for stepper motor



// Define the stepper motor and the pins that is connected to
AccelStepper stepper1(1, stepPin, dirPin); // (Type of driver: with 2 pins, STEP, DIR)

void setup() {
  // Setup output status LEDs
  pinMode(LED_tracking, OUTPUT);
  pinMode(LED_OFF, OUTPUT);
  pinMode(LED_slewing, OUTPUT);

  // Setup for rotary encoder
  Serial.begin(9600);
  pinMode(encoderDT, INPUT_PULLUP);
  pinMode(encoderCLK, INPUT_PULLUP);
  pinMode(encoderSW, INPUT_PULLUP);
  attachInterrupt(digitalPinToInterrupt(encoderCLK), calcSpeed, CHANGE);
  previousDT_val = digitalRead(encoderDT);
  previousCLK_val = digitalRead(encoderCLK);
  previousSW_val = digitalRead(encoderSW);  

  // Setup for input buttons
  pinMode(slewing_SW, INPUT);
  pinMode(tracking_SW, INPUT);
  
  previous_slewing_SW_val = digitalRead(slewing_SW);
  previous_tracking_SW_val = digitalRead(tracking_SW);

  // Setup LEDs
  int slewing_SW_val = digitalRead(slewing_SW); 
  int tracking_SW_val = digitalRead(tracking_SW); 
  initializeMode(slewing_SW_val,tracking_SW_val);

  // Set maximum speed value for the stepper
  stepper1.setMaxSpeed(max_steps_per_second);    
}

void loop() {
  int actualSW_val = digitalRead(encoderSW); 
  int slewing_SW_val = digitalRead(slewing_SW); 
  int tracking_SW_val = digitalRead(tracking_SW); 

  if (slewing_SW_val != previous_slewing_SW_val || tracking_SW_val != previous_tracking_SW_val || actualSW_val != previousSW_val) {
    initializeMode(slewing_SW_val,tracking_SW_val);
        
    previous_tracking_SW_val = tracking_SW_val;
    previous_slewing_SW_val = slewing_SW_val;
    previousSW_val = actualSW_val;
  }

  stepper1.setSpeed(steps_per_second);
  stepper1.runSpeed();

}



void calcSpeed()
{
  int actualCLK = digitalRead(encoderCLK);
  int actualEncoderDT = digitalRead(encoderDT);
  int slewing_SW_val = digitalRead(slewing_SW); 
  int tracking_SW_val = digitalRead(tracking_SW); 

  if (slewing_SW_val && !tracking_SW_val) { // TRACKING MODE
    if ((actualCLK == 1) and (previousCLK_val == 0))
    {
      if (actualEncoderDT == 1)
        steps_per_second=steps_per_second-0.5*tracking_rotary_change_sps;
      else
        steps_per_second=steps_per_second+0.5*tracking_rotary_change_sps;
    }

    if ((actualCLK == 0) and (previousCLK_val == 1))
    {
      if (actualEncoderDT == 1)
        steps_per_second=steps_per_second+0.5*tracking_rotary_change_sps;
      else
        steps_per_second=steps_per_second-0.5*tracking_rotary_change_sps;
    }
  }
  else if (!slewing_SW_val && tracking_SW_val) { // SLEWING MODE
    if ((actualCLK == 1) and (previousCLK_val == 0))
    {
      if (actualEncoderDT == 1)
        steps_per_second=steps_per_second-0.5*slewing_rotary_change_sps;
      else
        steps_per_second=steps_per_second+0.5*slewing_rotary_change_sps;
    }

    if ((actualCLK == 0) and (previousCLK_val == 1))
    {
      if (actualEncoderDT == 1)
        steps_per_second=steps_per_second+0.5*slewing_rotary_change_sps;
      else
        steps_per_second=steps_per_second-0.5*slewing_rotary_change_sps;
    }
  }    

  // Set correct direction for rotation
  if (steps_per_second < 0)
  {
    digitalWrite(dirPin,HIGH); //Changes the rotation backwards
  }
  if (steps_per_second > 0)
  {
    digitalWrite(dirPin,LOW); //Changes the rotation forward
  }  

  // Enforce maximum speed of rotation
  if (steps_per_second > max_steps_per_second)
  {
    steps_per_second = max_steps_per_second;
  } else if (steps_per_second < -max_steps_per_second) {
    steps_per_second = -max_steps_per_second;
  }

  Serial.print(steps_per_second);
  Serial.println(" steps/sec");

  previousCLK_val = actualCLK;
}

void initializeMode(int slewing_SW_val,int tracking_SW_val)
{

  if (slewing_SW_val && tracking_SW_val){ // OFF
      digitalWrite(LED_tracking, LOW);
      digitalWrite(LED_OFF, HIGH);
      digitalWrite(LED_slewing, LOW);
      Serial.println("Motor turned off!");
      steps_per_second = 0;
    } 
    else if (slewing_SW_val && !tracking_SW_val) { // TRACKING MODE
      digitalWrite(LED_tracking, HIGH);
      digitalWrite(LED_OFF, LOW);
      digitalWrite(LED_slewing, LOW);
      Serial.println("Motor in tracking mode!");
      steps_per_second = sidereal_step_per_second;
    }
    else if (!slewing_SW_val && tracking_SW_val) { // SLEWING MODE
      digitalWrite(LED_tracking, LOW);
      digitalWrite(LED_OFF, LOW);
      digitalWrite(LED_slewing, HIGH);
      Serial.println("Motor in slewing mode!");
      steps_per_second = slewing_step_per_second;
    }    

    digitalWrite(dirPin,LOW); //Changes the rotation direction forward

}

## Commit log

2025-06-05 Updated readme and content
    [Gingerbread_label.stl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]
2025-06-05 Update README.md
    Added details of the EQ-13 mount.
